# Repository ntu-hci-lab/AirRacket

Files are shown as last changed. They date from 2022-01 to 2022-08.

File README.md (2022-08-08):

# AirRacket: Perceptual Design of Ungrounded, Directional Force Feedback to Improve Virtual Racket Sports Experiences

Ching-Yi Tsai, I-Lun Tsai, Chao-Jung Lai, Derrek Chow, Lauren Wei, Lung-Pan Cheng, Mike Yen Chen

CHI'22 Best Paper 🏆

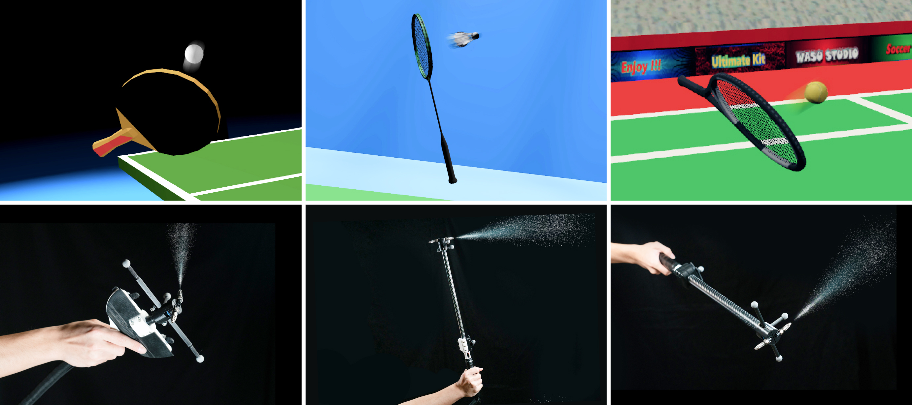
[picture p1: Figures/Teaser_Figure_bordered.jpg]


### Table of Contents  
- [System Diagram](#system-diagram)
- [Racket-shaped Handheld Devices](#racket-shaped-handheld-devices)
  - [Alternative Tracking System](#alternative-tracking-system)
  - [Additional Racket Sports](#additional-racket-sports)
- [Pneumatic Control System](#pneumatic-control-system)
  - [Pneumatic System Overview](#pneumatic-system-overview)
  - [Circuit Schematic](#circuit-schematic)
  - [Control Code](#code)
    - [Arduino](#arduino)
    - [Unity](#unity) 
- [Website, Paper/Video Links and BibTeX](#reference)

<a name="system-diagram"/>

## System Diagram

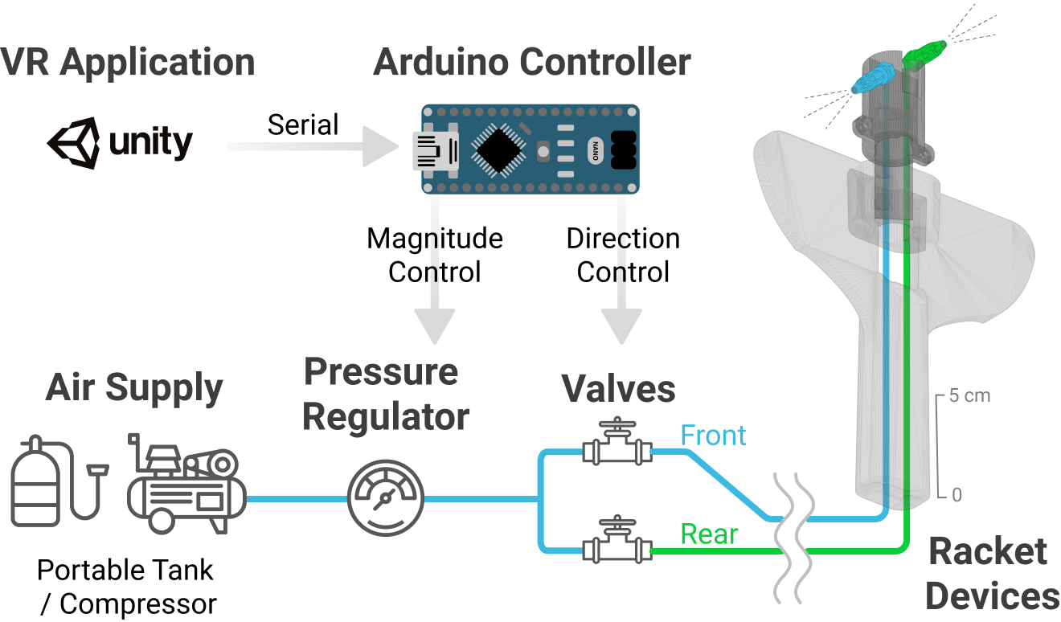
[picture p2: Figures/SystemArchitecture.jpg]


AirRacket system includes: (1) Custom-designed racket devices: Two nozzles with separate tubing mounted on sport-specific handle and shaft, and (2) Pneumatic control system: a pressure regulator controlling force magnitude and two solenoid valves controlling force direction.

<a name="racket-shaped-handheld-devices"/>

# Racket-shaped Handheld Devices

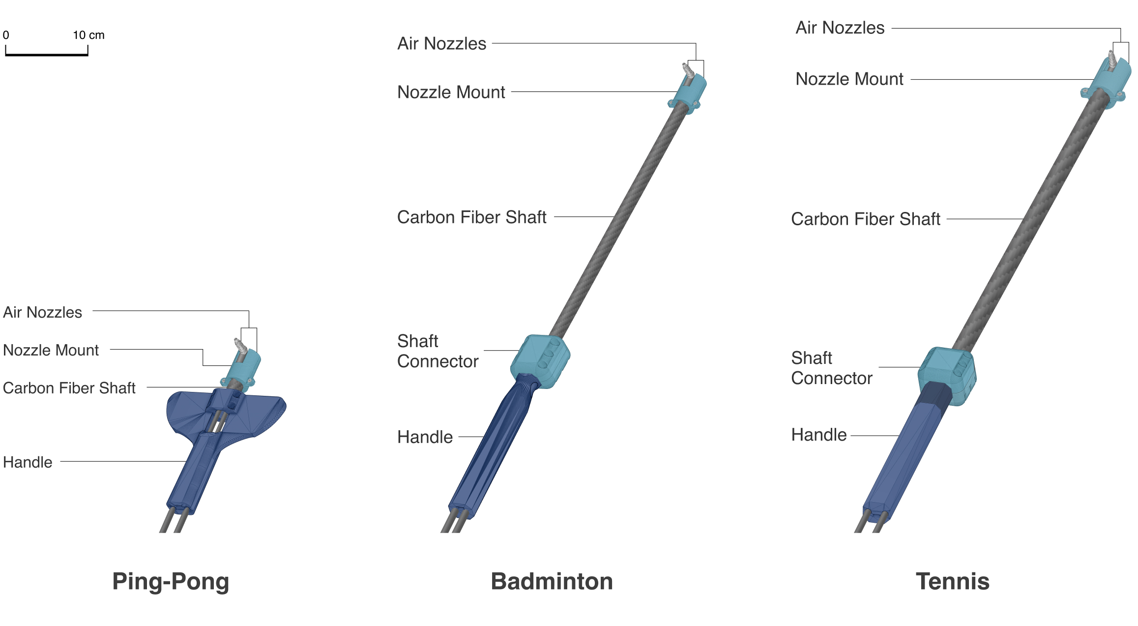
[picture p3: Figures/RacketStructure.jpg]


Each of our handhheld devices consists of a 3D-printed handle, a carbon fiber shaft (ø14mm or ø 23mm outer-diameter), and two noise-reducing nozzles on a 3D-printed nozzle mount. 
The 3D-models in the `./3D Racket Model` folder includes:
1. Racket-shaped Handle: components with specific shapes modelled after real rackets handles with a cuboid-shaped hole for placing LRA vibrator and tunnels for low-friction polyurethane tubing (ø6mm),
2. Shaft connector: components that connect the carbon fiber stick and racket-shaped handle by clamping them (to compensate margin error due to 3D printing resolution, appplying adhesive or electrical tape "inside" the shaft connectors are recommended), and
3. Nozzle connector: components for mounting the nozzles and should be able to clamp the carbon fiber shaft (those additional branches are for adding reflective markers, but we also include file without them).

Notice: to complete the rest of the handheld device, compressed air nozzles, L-shape nozzle fittings, carbon fiber shaft, and PU tubes(ø6mm) are required. 

<a name="alternative-tracking-system"/>

### Alternative Tracking System
To be compatible with general VR systems, in `./3D Racket Model/ViveTracker Version/`, we also provides additional nozzle connectors (shaft connectors for badminton) for mounting ViveTrackers, which can be mounted as the below. However, the center-of-mass and total weight would deviate a lot with this current version. 

| OptiTrack | ViveTracker |
| :---: | :---: |
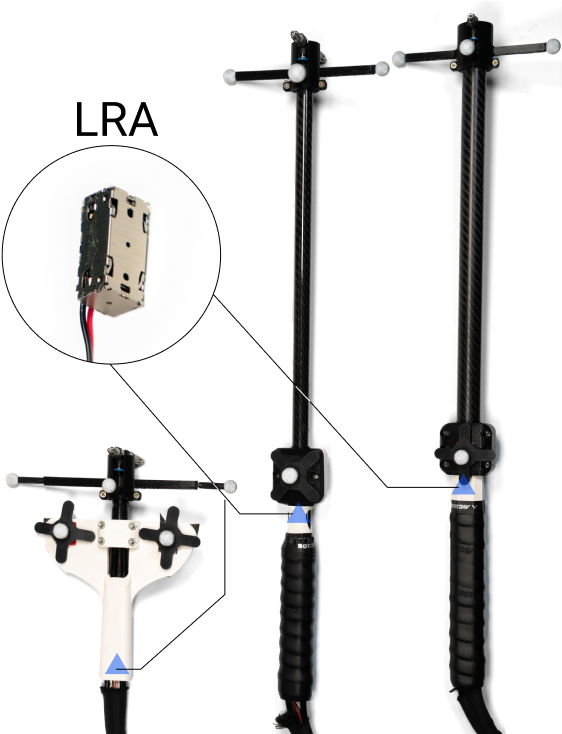
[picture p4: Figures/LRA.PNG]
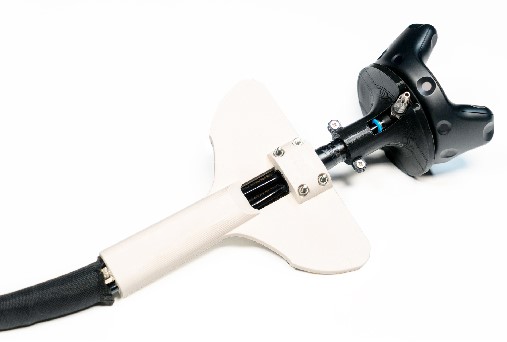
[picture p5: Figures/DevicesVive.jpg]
|  |  |

<a name="additional-racket-sports"/>

### Additional Racket Sports
Besides the three racket sports (pingpong/badminton/tennis) we demonstrated and experimented in our paper, we also put some additional racket sports design in the `./3D Racket Model/Other Raccket Sports/`, including designs for baseball, hockey, golf, racquet ball, and a sword.

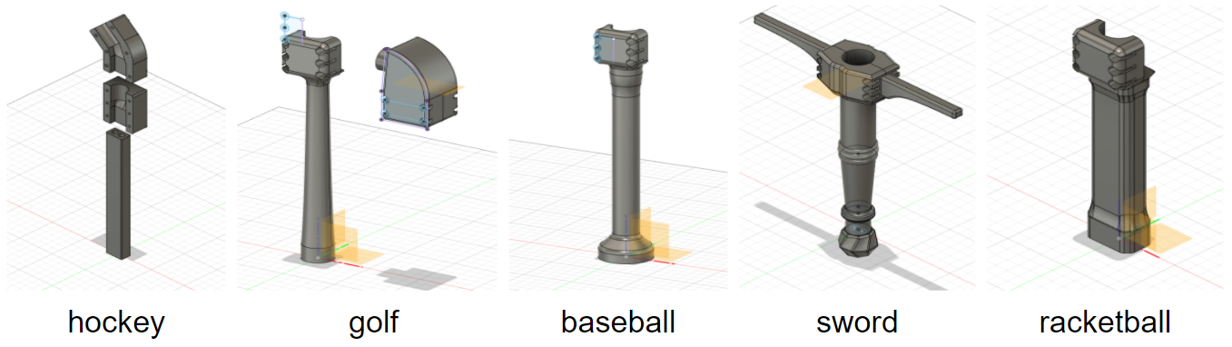
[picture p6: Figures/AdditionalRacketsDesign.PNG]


<a name="pneumatic-control-system"/>

## Pneumatic Control System

<a name="pneumatic-system-overview"/>

### Pneumatic System Overview
Below is what our handheld devices and pneumatic system combined looks like.
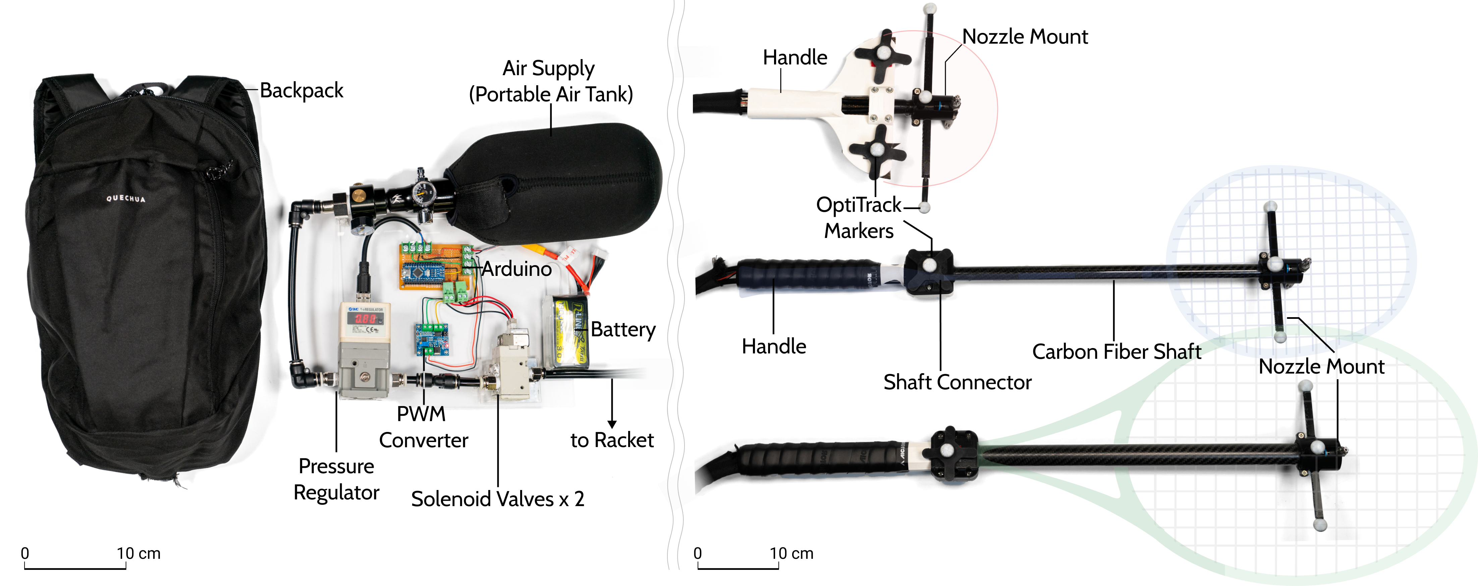
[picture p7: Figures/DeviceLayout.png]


<a name="circuit-schematic"/>

### Circuit Schematic


<a name="code"/>

### Control Code

<a name="arduino"/>

#### Arduino
We include the compiled code on our Arduino board at `./Code/AirRacket.ino`.

<a name="unity"/>

#### Unity
The specific communicating protocols are written in `./Code/ArduinoBasic.cs` and `./Code/ArduinoControl.cs`, which we attached on Unity GameObject in our virtual scene.

<a name="reference"/>

## Website, Paper/Video Links and BibTeX
[DOI](https://doi.org/10.1145/3491102.3502034), [Video Preview](https://www.youtube.com/watch?v=UAoQlSbQRYY), [Video Presentation](https://www.youtube.com/watch?v=INXk8tT5H3U)
### BibTex
```
@inproceedings{10.1145/3491102.3502034,
author = {Tsai, Ching-Yi and Tsai, I-Lun and Lai, Chao-Jung and Chow, Derrek and Wei, Lauren and Cheng, Lung-Pan and Chen, Mike Y.},
title = {AirRacket: Perceptual Design of Ungrounded, Directional Force Feedback to Improve Virtual Racket Sports Experiences},
year = {2022},
isbn = {9781450391573},
publisher = {Association for Computing Machinery},
address = {New York, NY, USA},
url = {https://doi.org/10.1145/3491102.3502034},
doi = {10.1145/3491102.3502034},
abstract = {We present AirRacket, perceptual modeling and design of ungrounded, directional force feedback for virtual racket sports. Using compressed air propulsion jets to provide directional impact forces, we iteratively designed for three popular sports that span a wide range of force magnitudes: ping-pong, badminton, and tennis. To address the limited force magnitude of ungrounded force feedback technologies, we conducted a perception study which discovered the novel illusion that users perceive larger impact force magnitudes with longer impact duration, by an average factor of 2.57x. Through a series of formative, perceptual, and user experience studies with a combined total of 72 unique participants, we explored several perceptual designs using force magnitude scaling and duration scaling methods to expand the dynamic range of perceived force magnitude. Our user experience evaluation showed that perceptual designs can significantly improve realism and preference vs. physics-based designs for ungrounded force feedback systems.},
booktitle = {CHI Conference on Human Factors in Computing Systems},
articleno = {185},
numpages = {15},
keywords = {air propulsion, ungrounded force feedback, Haptics, perceptual design, virtual reality., force perception},
location = {New Orleans, LA, USA},
series = {CHI '22}
}
```

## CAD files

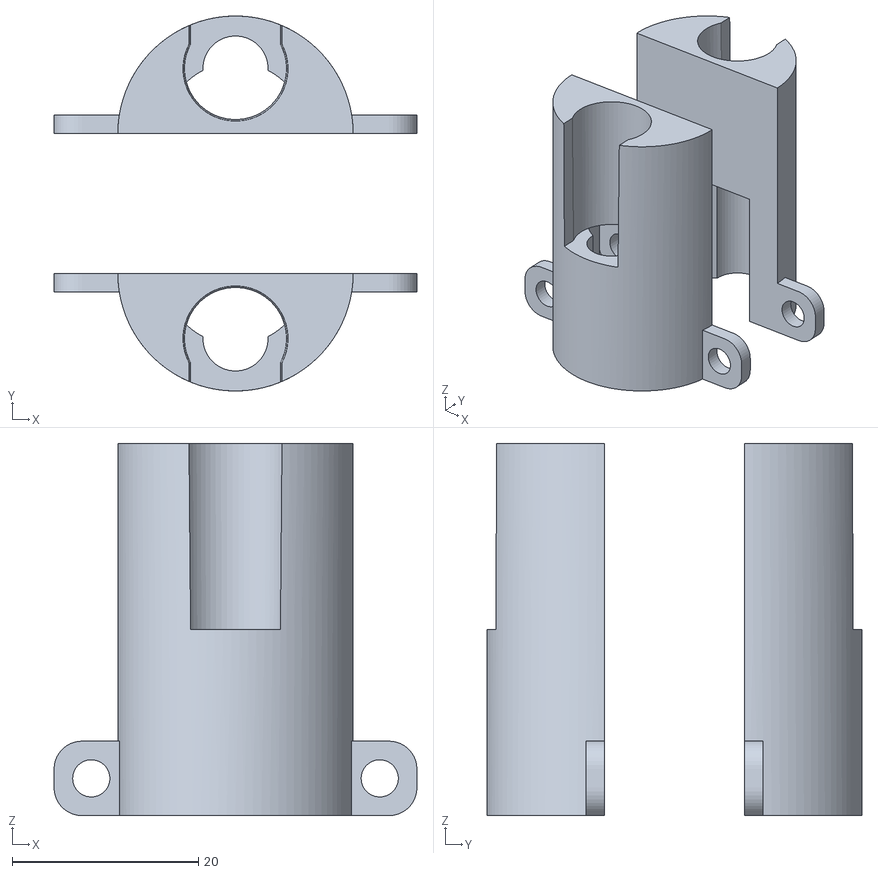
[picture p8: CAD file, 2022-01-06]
3D Racket Model/Badminton/Badminton nozzle connector (no marker mount).stl
39.0 x 40.3 x 40.0

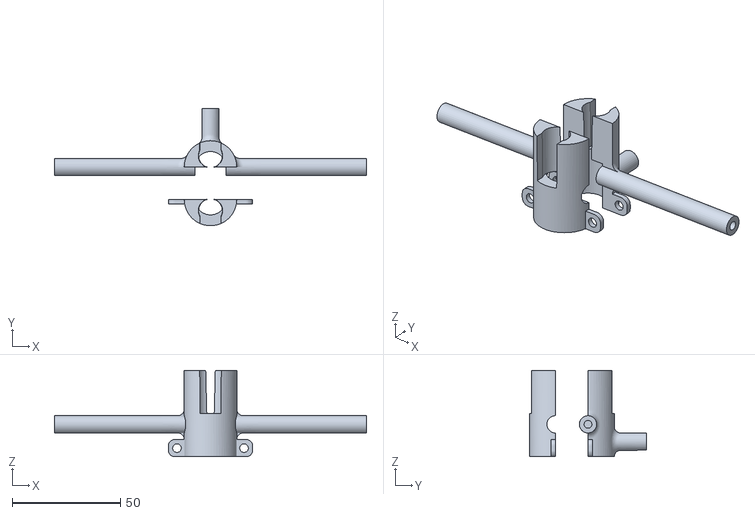
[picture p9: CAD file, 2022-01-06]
3D Racket Model/Badminton/Lighter Badminton Version/Badminton nozzle connector (14mm).stl
144.3 x 54.3 x 40.0

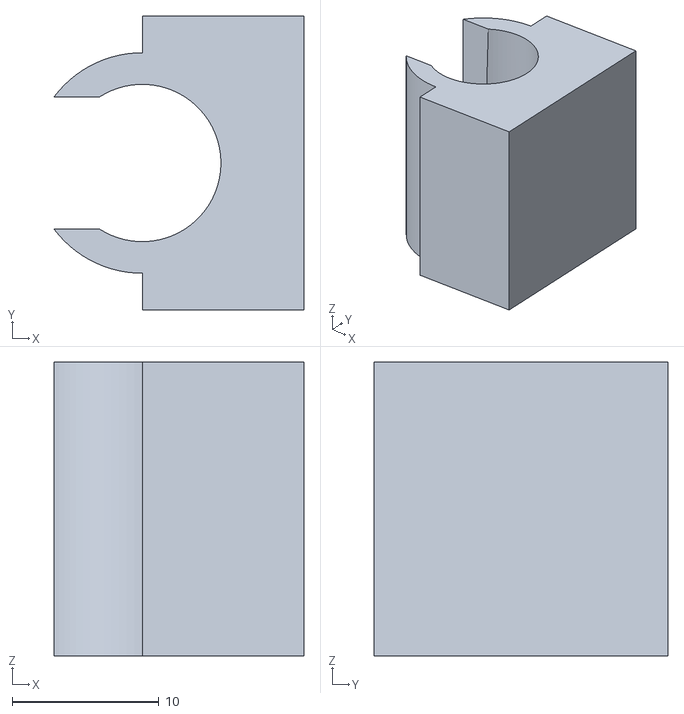
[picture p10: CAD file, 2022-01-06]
3D Racket Model/L-shape Nozzle Fitting Connector Prototype.stl
17.0 x 20.0 x 20.0

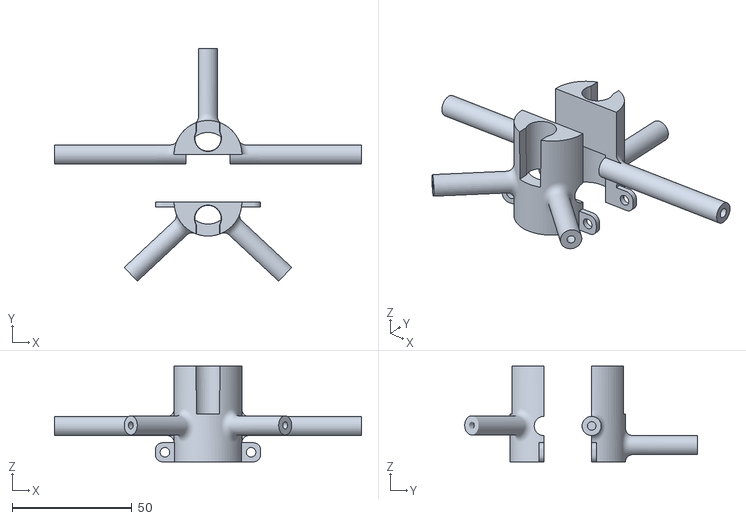
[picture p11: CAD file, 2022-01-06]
3D Racket Model/Other Raccket Sports/Baseball/Baseball nozzle connector (18mm).stl
128.3 x 97.2 x 40.0

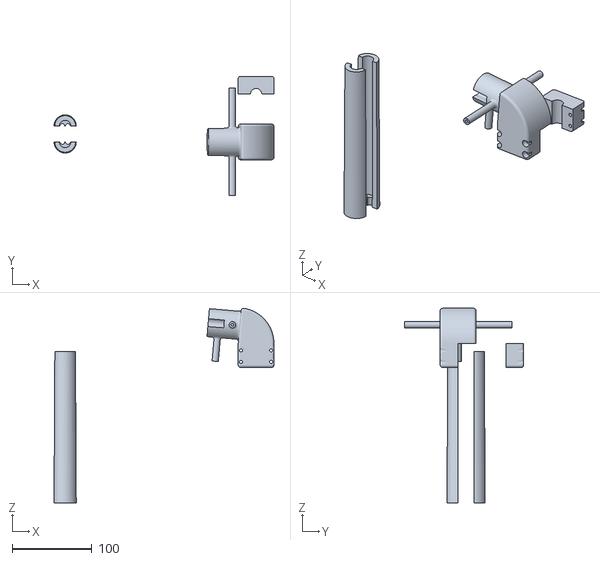
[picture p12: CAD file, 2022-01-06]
3D Racket Model/Other Raccket Sports/Golf/Golf handle with nozzle connector.f3d.stl
276.5 x 150.2 x 244.5

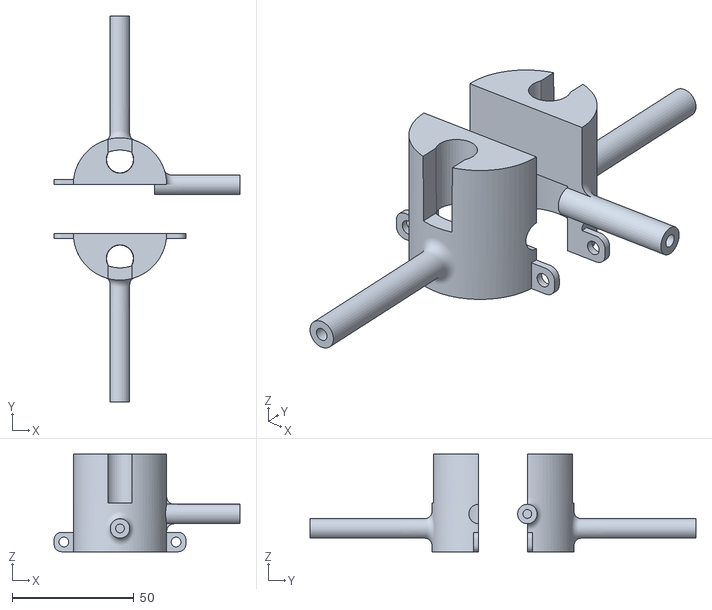
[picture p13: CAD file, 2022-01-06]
3D Racket Model/Other Raccket Sports/Hockey/Hockey nozzle connector.stl
76.2 x 158.3 x 40.0

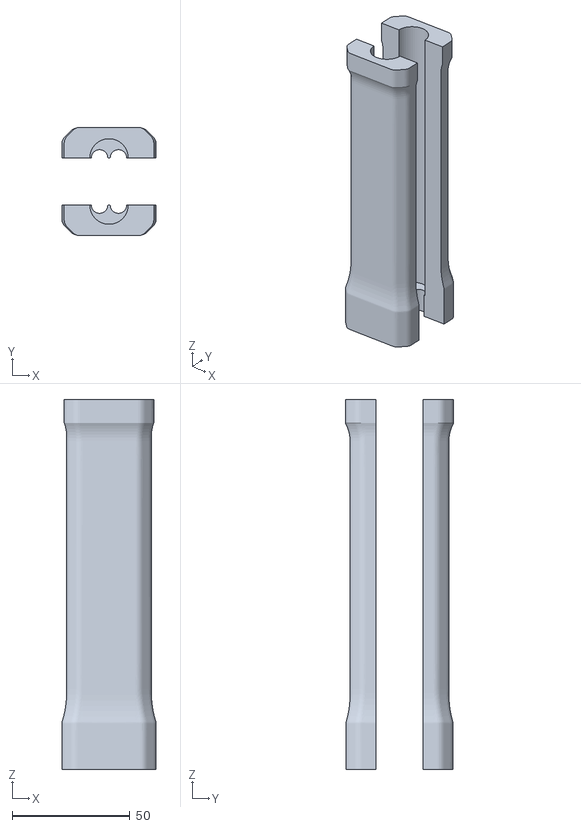
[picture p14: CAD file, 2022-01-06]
3D Racket Model/Other Raccket Sports/Racquet Ball/Racquet ball handle.stl
40.0 x 46.0 x 157.0

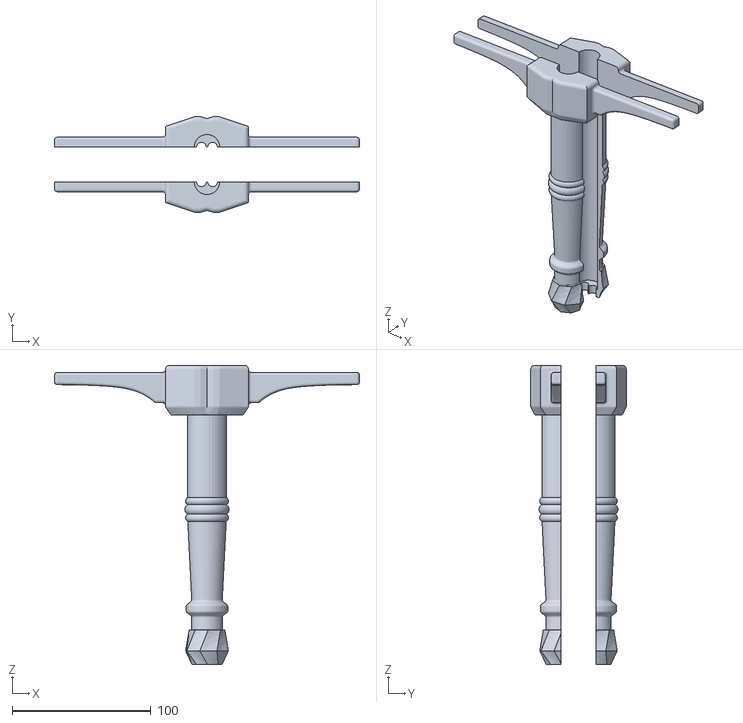
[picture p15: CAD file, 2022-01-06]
3D Racket Model/Other Raccket Sports/Sword/Sword handle.stl
220.0 x 69.0 x 216.0

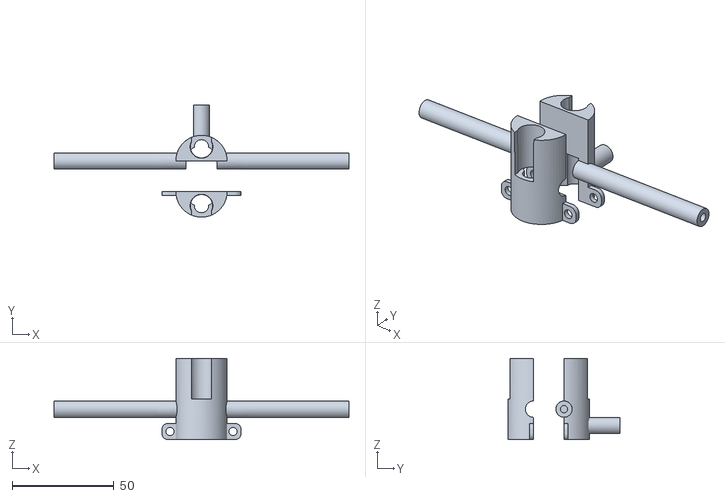
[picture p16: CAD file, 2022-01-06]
3D Racket Model/Pingpong/Pinpong nozzle connector.stl
145.3 x 55.3 x 40.0

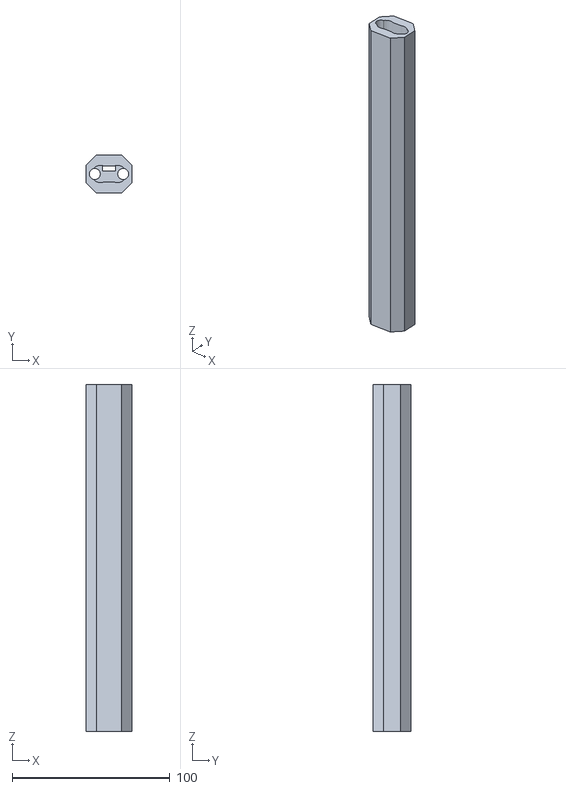
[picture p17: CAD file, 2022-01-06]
3D Racket Model/Tennis/Tennis handle.stl
29.0 x 24.0 x 220.0

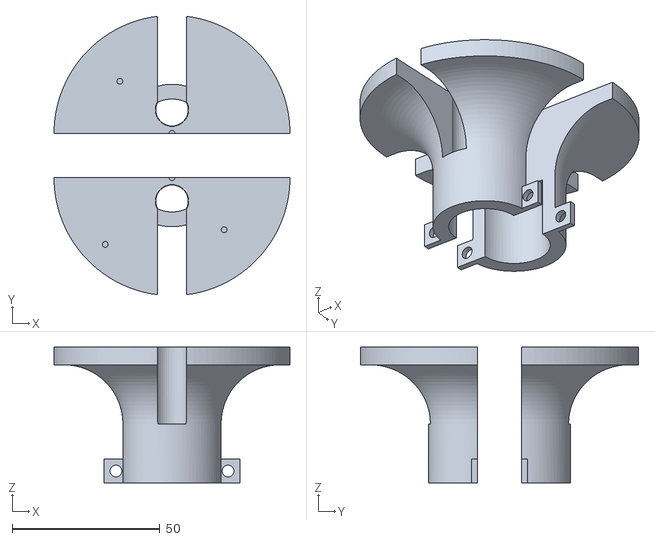
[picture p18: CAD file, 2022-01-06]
3D Racket Model/ViveTracker Version/Tennis nozzle connector for ViveTracker.stl
80.0 x 94.4 x 46.0

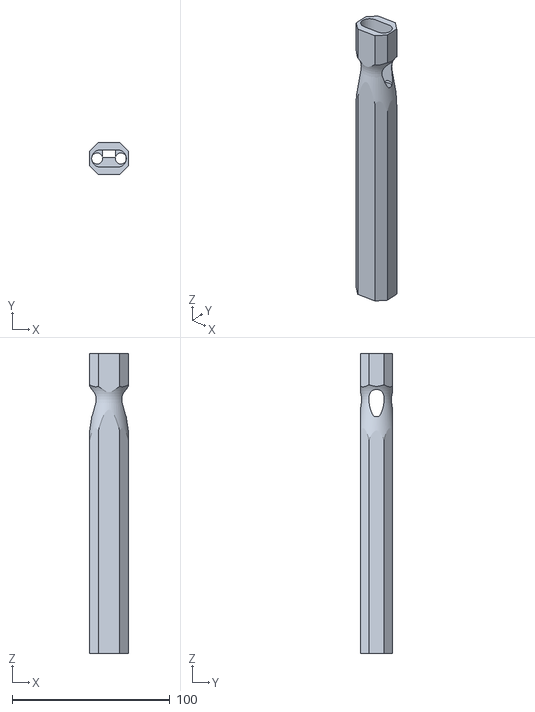
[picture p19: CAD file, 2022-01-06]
3D Racket Model/Badminton/Badminton handle.stl
24.5 x 20.5 x 190.0

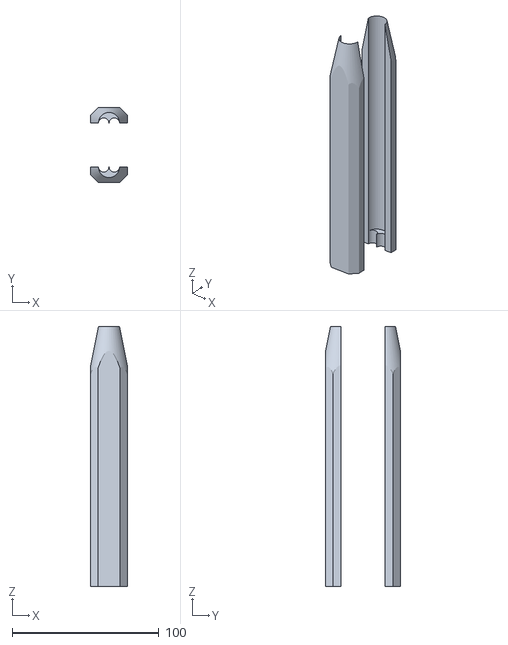
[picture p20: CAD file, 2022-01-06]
3D Racket Model/Badminton/Lighter Badminton Version/Badminton handle (without shaft connector).stl
25.0 x 51.0 x 177.1

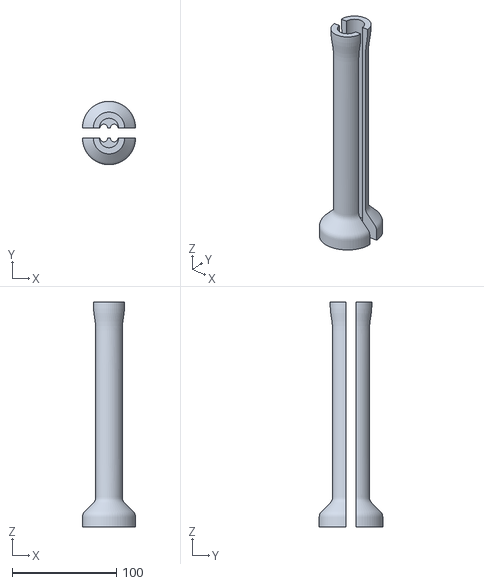
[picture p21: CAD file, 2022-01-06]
3D Racket Model/Other Raccket Sports/Baseball/Baseball Handle.stl
50.8 x 60.8 x 215.4

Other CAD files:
3D Racket Model/Other Raccket Sports/Hockey/Hockey shaft connectors.stl
3D Racket Model/Other Raccket Sports/Racquet Ball/Racquet nozzle connector.stl
3D Racket Model/Other Raccket Sports/Sword/Sword nozzle connector.stl
3D Racket Model/Badminton/Badminton handle.f3d
3D Racket Model/Badminton/Badminton nozzle connector (no marker mount).f3d
3D Racket Model/Badminton/Badminton nozzle connector.f3d
3D Racket Model/Badminton/Badminton nozzle connector.stl
3D Racket Model/Badminton/Badminton shaft connector.f3d.f3d
3D Racket Model/Badminton/Badminton shaft connector.f3d.stl
3D Racket Model/Badminton/Lighter Badminton Version/Badminton handle (without shaft connector).f3d
3D Racket Model/Badminton/Lighter Badminton Version/Badminton nozzle connector (14mm).f3d
3D Racket Model/L-shape Nozzle Fitting Connector Prototype.f3d
3D Racket Model/Other Raccket Sports/Baseball/Baseball Handle.f3d
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

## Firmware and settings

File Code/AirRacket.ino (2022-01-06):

#include <Wire.h>
#include "Adafruit_DRV2605.h"
int intensity = 100;
int vibe_duration = 30; 
int riseTime = 0;

int force_pin = 5;
int valve_pin_0 = 6;
int valve_pin_1 = 7;
int led_pin = 13;

//default configuration
int air_duration = 40;
int force = 0;

//
int currentMillis;
int startFireTime = 0;

Adafruit_DRV2605 drv;
void tcaselect() {
  Wire.beginTransmission(0x70);
  Wire.write(0x03);
  Wire.endTransmission();
}
void setup() {
  Serial.begin(115200);
  Serial.println("DRV test");
  Wire.begin();
  tcaselect();
  drv.begin();
  drv.useLRA();
  drv.writeRegister8(DRV2605_REG_CONTROL3, drv.readRegister8(DRV2605_REG_CONTROL3) | 0x01);
  drv.setMode(DRV2605_MODE_REALTIME);
  Serial.begin(115200);
  pinMode(force_pin, OUTPUT);
  pinMode(valve_pin_0, OUTPUT);
  pinMode(valve_pin_1, OUTPUT);
  pinMode(led_pin, OUTPUT);
}

uint8_t rtp_index = 0;
uint8_t rtp[] = {
  0x30, 100
};
void loop() {
  analogWrite(force_pin, force);
  currentMillis = millis();
  if(Serial.available()>0){
    char cmd = Serial.read();
    if(cmd == 'f'){
      fireStart(valve_pin_0);
    }
    else if(cmd == 'b'){
      fireStart(valve_pin_1);  
    }
    else if(cmd == 'v'){
      vibeStart();  
    }
    else if(cmd == 'c'){
      configForce();
    }
    else if(cmd == 'm') {
      configVibe();
    }
    //Serial.flush();
  }
}

//fire the air jet
void fireStart(int valve_pin){
  digitalWrite(valve_pin, HIGH);
  digitalWrite(led_pin, HIGH);
  delay(air_duration);
  digitalWrite(valve_pin, LOW);
  digitalWrite(led_pin, LOW);
}

void vibeStart(){
   drv.setRealtimeValue(intensity);
    delay(vibe_duration);
    drv.setRealtimeValue(0x00);
}

void configForce(){
  force = parseData();
  air_duration = parseTime();
  
  analogWrite(force_pin, force);
  
  Serial.print("Read");
  Serial.print(" f: ");
  Serial.print(force);
  Serial.print(" d: ");
  Serial.println(air_duration);
}

void configVibe(){
  intensity = parseData();
  vibe_duration = parseTime();
  Serial.print("VibeRead");
  Serial.print(" f: ");
  Serial.print(intensity);
  Serial.print(" d: ");
  Serial.println(vibe_duration);
}

int parseData(){
  String num = "";
  char c;
   for(int i = 0; i < 3; i++){
      while(true){
        if(Serial.available()){
          c = Serial.read();
          break;
        }
      }
      num += c;
   }
   return num.toInt();
}

int parseTime(){
  String num = "";
  char c;
   for(int i = 0; i < 4; i++){
      while(true){
        if(Serial.available()){
          c = Serial.read();
          break;
        }
      }
      num += c;
   }
   return num.toInt();
}

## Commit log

2022-01-06 arduino code initial upload
2022-01-06 CSharp code for arduino control in Unity added
2022-01-06 Initial Upload for all stl and f3d files
    [Badminton handle (without shaft connector).f3d, Badminton handle (without shaft connector).stl, Badminton handle.f3d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]
